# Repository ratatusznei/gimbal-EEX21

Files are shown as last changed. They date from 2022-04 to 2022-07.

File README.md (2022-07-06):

# Sistema estabilizador de dois eixos para câmera - Gimbal

###### Autores em ordem alfabética
[Fernando](https://github.com/ratatusznei)

[Henrique](https://github.com/HenriqueKnapp)

[Robson](https://github.com/robson1622)

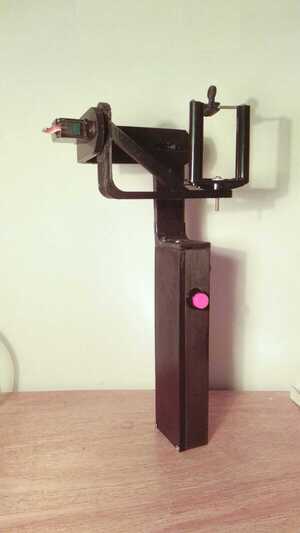
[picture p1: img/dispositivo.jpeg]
Dispositivo montado sem celular


Foto do dispositivo montado sem o celular no suporte.

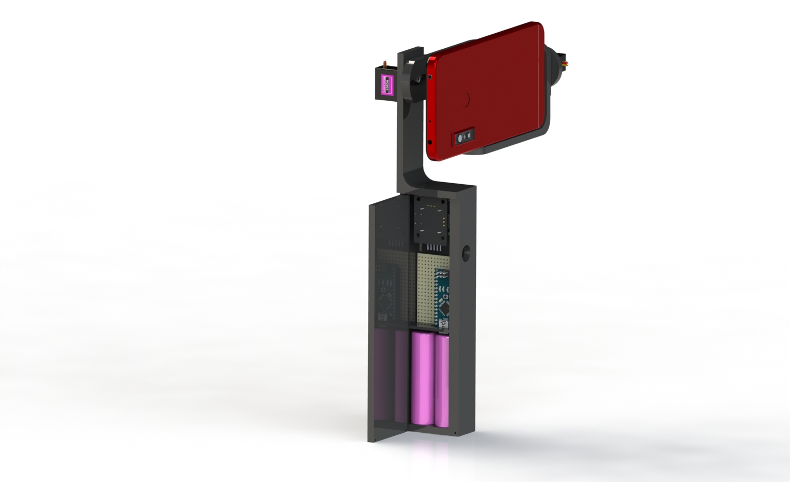
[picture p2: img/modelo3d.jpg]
Modelo 3d


Renderização de modelo montado em computador, mostrando a placa de circuitos e as baterias internas.

## O que é?
É um dispositivo que procura manter a orientação de uma câmera ou celular fixa, compensando possíveis variações que podem ocorrer durante a gravação de um vídeo ou fotografia. O sistema estabiliza nos eixos X e Y conforme a figura:

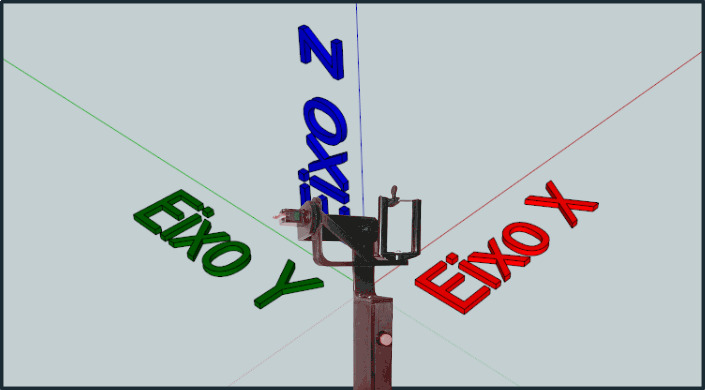
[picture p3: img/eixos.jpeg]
Estabilizador no espaço 3d Eixos de atuação X e Y


## Como funciona?
O sistema contrói uma representação interna da orientação do dispositivo em relação à direção da gravidade com base nas leituras de dois sensores giroscópio e acelerômetro. Então utilizando de dois motores atuando sobre a orientação da câmera a gravação é estabilizada.

## Casos de uso
Além de servir como estabilizador para câmeras, esse sistema pode ser readequado para uso em robôs sensíveis à orientação, drones ou em aplicações de realidade virtual capturando a orientação de um objeto no mundo real.

## Mais detalhes
Para mais detalhes e referências sobre o projeto, verifique o [relatório final nesse mesmo repositório](https://github.com/ratatusznei/gimbal-EEX21/blob/master/relatorio/pdfs/EEX21_Equipe5_Relatorio_EstabilizadorDeDoisEixosPraCameras.pdf).

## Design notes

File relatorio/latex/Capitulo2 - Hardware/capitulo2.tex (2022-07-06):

%%%% CAPÍTULO 2 - REVISÃO DA LITERATURA (OU REVISÃO BIBLIOGRÁFICA, ESTADO DA ARTE, ESTADO DO CONHECIMENTO)
%%
%% O autor deve registrar seu conhecimento sobre a
%% literatura básica do assunto, discutindo e 
%% comentando a informação já publicada. A revisão deve
%% ser apresentada, preferencialmente, em ordem
%% cronológica e por blocos de assunto, procurando
%% mostrar a evolução do tema.

%% Título e rótulo de capítulo (rótulos não devem conter caracteres especiais, acentuados ou cedilha)
\chapter{Hardware}\label{cap:revisaodaliteratura}

 Para a construção do projeto, foram utilizados os componentes listados na tabela 1, além de ferramentas como ferro de solda, percloreto de ferro etc.

\begin{table}[H]
\centering
\begin{tabular}{l|j|j}
Componente & Modelo/especificações & Quantidade \\\hline
Arduino & Nano & 1 \\
Baterias recarregáveis & INR18650-30Q & 2\\
ServoMotores & MG90s & 2\\
Joystick analógico & 3 Eixos KY-023 & 1\\
Interruptor Push Button & Retenção PBS-11A (127v) & 1\\
Regulador de tensão & LM7805 & 1\\
Acelerômetro e giroscópio & MPU-6050 & 1\\
Dissipador de alumínio & & 1\\
Barramentos & Macho e Fêmea 10 cm & 2\\
Cabo flat & 10 vias, 20 cm & 1\\
Espaguete termo retrátil & 20 cm & 1\\
Placa de fenolite & (Não perfurada) & 1\\ 
Filamento para impressora 3D & & \\
Parafusos & 8 mm & 10\\
\end{tabular}
\caption{\label{tab:widgets}Tabela de componentes e materiais utilizados na construção do dispositivo.}
\end{table}

\section{Modelagem e impressão 3D}
Todo o hardware do dispositivo está montado em uma estrutura impressa em 3D, as peças da estrutura da caixa (paredes e tampa) foram impressas ocas e com o filamento PLA que é mais frágil e leve se comparado ao material utilizado na impressão do suporte articulado, as peças do suporte articulado foram reforçadas sendo parcialmente impressas de forma maciça e produzidas com o filamento ABS ,que apresenta maior resistência, isto para suportar o peso do equipamento que será anexado à base da estrutura articulada. As dimensões das peças impressas em 3d foram definidas a partir de modelos dos componentes e também do circuito produzidos no software KiCad e SolidWorks, como pode ser visto nas figuras 1 e 2. 

\begin{figure}[H]
\centering
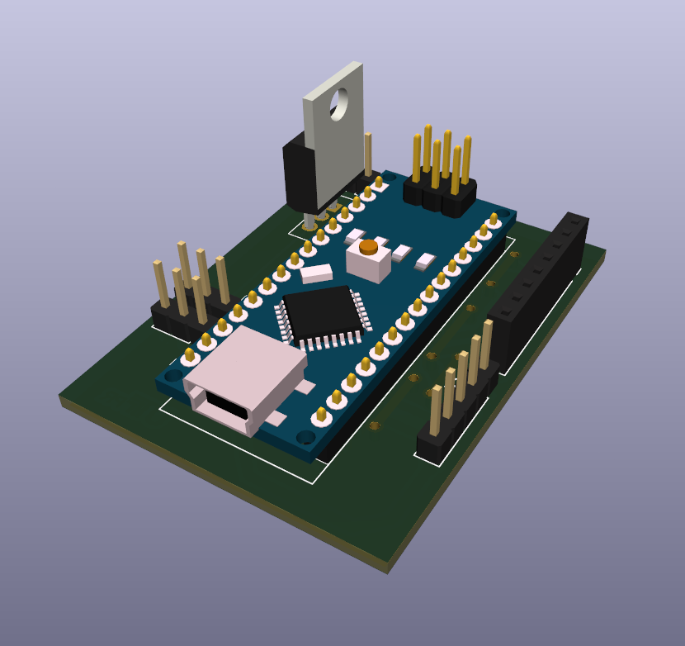
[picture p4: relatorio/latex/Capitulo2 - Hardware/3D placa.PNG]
\\
\caption{\label{fig:widgets}Modelo 3D da placa de circuito impresso.}
\end{figure}

\begin{figure}[H]
\centering
\\
\caption{\label{fig:widgets}Modelo 3D do dispositivo.}
\end{figure}

\section{Suporte articulado}
A estabilização para o equipamento preso à estrutura articulada é dada por dois eixos de rotação, estes possibilitam variar a inclinação do suporte na vertical e na horizontal de zero a 90 graus para cada lado, isto devido a cada servo motor MG90s possibilitar uma rotação de 180 graus. Cada servo motor opera entre 4,8 e 6 volts, com seu torque e velocidade de operação variando de acordo com esses parâmetros. Para um funcionamento estável, os motores não são alimentados pelo arduino, a tensão máxima fornecida aos dois servos é de 5 volts, como a tensão de saída do conjunto de baterias é de 7,2 volts, foi utilizado um regulador de tensão LM7805, que mantém uma tensão estável de 5 volts se a tensão de entrada for maior que 7 volts, não excedendo 30 volts, isso nos dá os parâmetros da tabela 2.

\begin{table}[H]
\centering
\begin{tabular}{j|j|j}
Tensão de entrada & Torque & Velocidade de operação \\\hline
4,8 & 1,8kg/cm & 0.1sec/60 graus\\
5,0 & 1,9kg/cm & 0.1sec/60 graus\\
6,0 & 2,2kg/cm & 0.08sec/60 graus\\
\end{tabular}
\caption{\label{tab:widgets}Tabela de parâmetros do servo motor MG90s para diferentes tensões de entrada.}
\end{table}

Ambos os servos são fixados diretamente na estrutura impressa por meio de dois parafusos, e as peças móveis da estrutura articulada são encaixadas diretamente no eixo de cada um dos servos com o auxilio de hélices de plástico. Para facilitar a movimentação das partes móveis e diminuir o atrito, e por consequência o desgaste do material plástico, foi adicionado sob cada eixo (encontro de duas partes móveis) duas arruelas de ferro com graxa. O cabeamento dos dois servos segue presa às estruturas móveis da estrutura articulada, isso devido ao comprimento necessário dos cabos ser diferente para diferentes posições de operação.

\section{Eletrônica}
%incluir esquematico, diagrama de blocos
O sistema conta com duas células (baterias) recarregáveis de 3,6 volts e 3000 mAh ligadas em série, fornecendo ao sistema 7,2 volts, este conjunto de baterias é ligado a um interruptor, e este é ligado à placa de circuitos. A trilha positiva se liga ao regulador de tensão LM7805 (que manda cerca de 5,0 volts aos dois servo motores), e também ao arduino nano (este não precisa de um regulador de tensão externo, como no caso dos dois servos, pois já possui um integrado em sua placa). O joystick analógico e o sensor MPU-6050 são conectados exclusivamente ao arduino conforme pode ser visto na figura 3. Todos os componentes são conectados por meio de barramentos soldados na placa, permitindo o funcionamento como pode ser visto na figura 4, dando ao sistema modularidade, uma vez que cada componente pode ser removido individualmente, facilitando operações como manutenção e ajustes.

\begin{figure}[H]
\centering
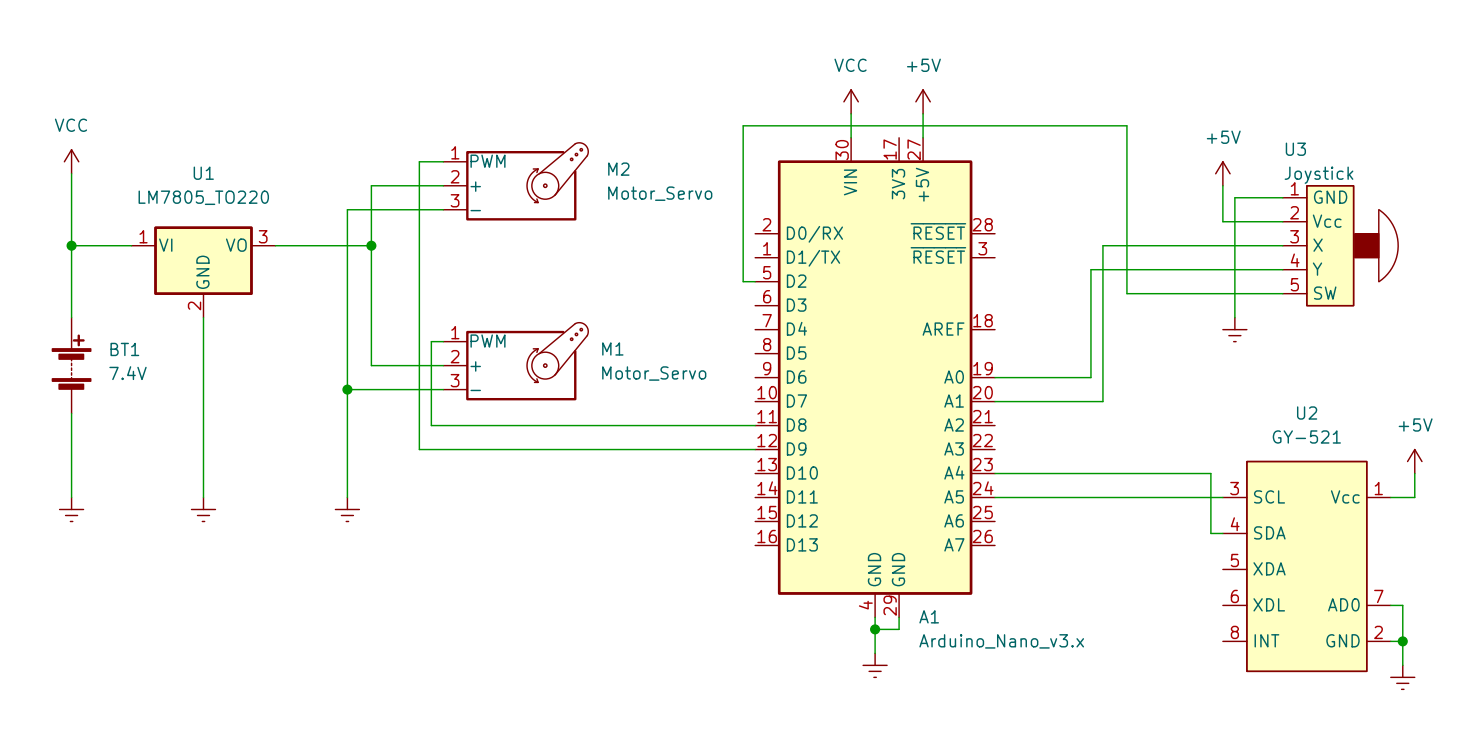
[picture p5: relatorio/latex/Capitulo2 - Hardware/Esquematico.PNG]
\\
\caption{\label{fig:widgets}Esquemático dos componentes eletrônicos.}
\end{figure}

\begin{figure}[H]
\centering
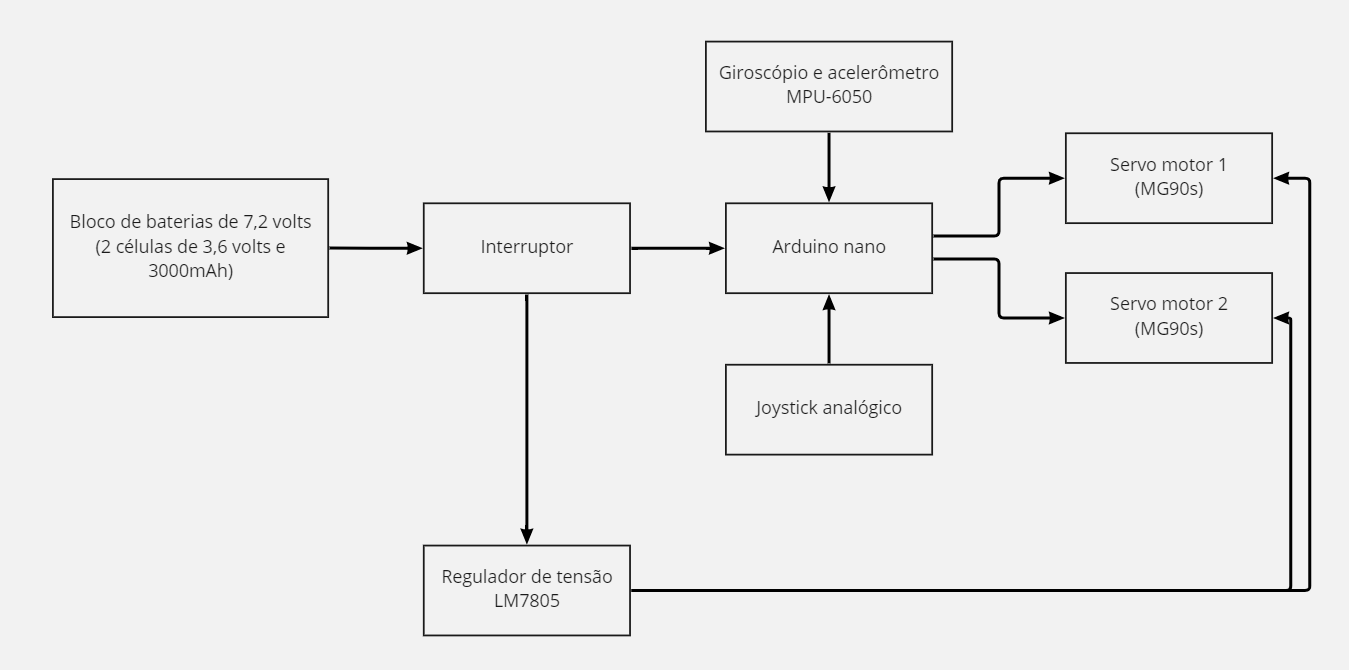
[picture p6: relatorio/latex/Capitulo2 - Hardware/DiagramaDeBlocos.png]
\\
\caption{\label{fig:widgets}Diagrama de blocos do dispositivo.}
\end{figure}

A placa de circuitos foi produzida manualmente pelos integrantes do grupo deste trabalho utilizando percloreto de ferro. A imagem do circuito foi produzida através do software KiCad, como pode ser visto na figura 5, e foi transferida de um papel fotográfico para a placa de fenolite utilizando uma fonte de calor, depois de resfriada, foi imersa em percloreto de ferro por cerca de cinco minutos. Após o fim do processo, obtivemos uma placa funcional do circuito do projeto, como pode ser visto na figura 6.

\begin{figure}[H]
\centering
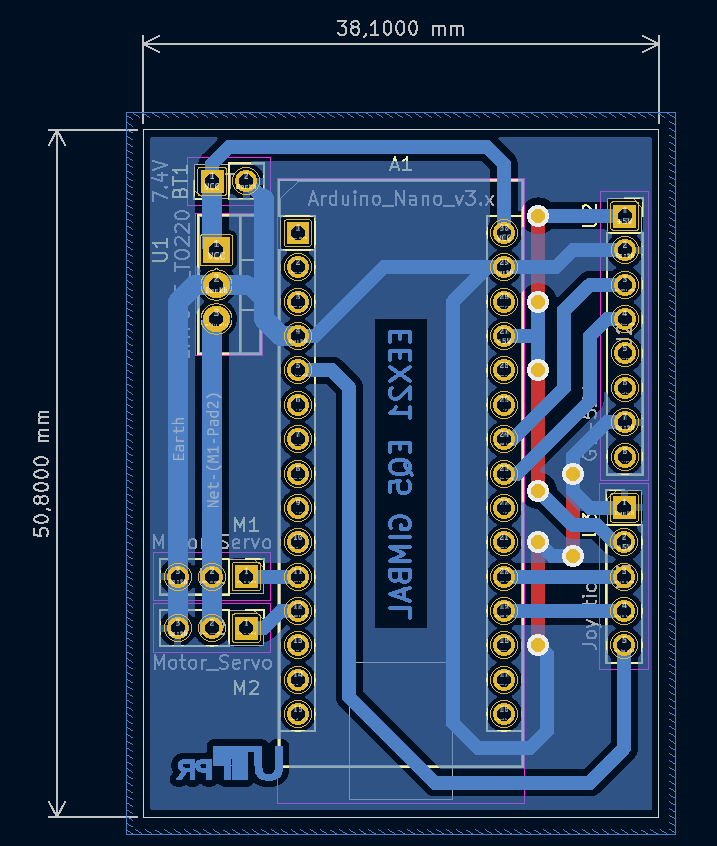
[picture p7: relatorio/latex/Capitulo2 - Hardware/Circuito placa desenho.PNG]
\\
\caption{\label{fig:widgets}Desenho do circuito no software KiCad.}
\end{figure}

\begin{figure}[H]
\centering
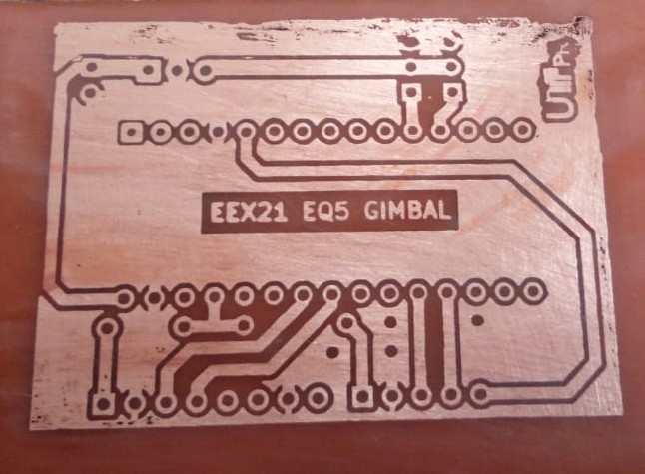
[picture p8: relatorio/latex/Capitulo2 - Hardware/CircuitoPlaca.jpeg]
\\
\caption{\label{fig:widgets}Placa produzida manualmente utilizando o processo de corrosão por percloreto de ferro.}
\end{figure}

Com exceção dos servo motores, os componentes são posicionados dentro da estrutura impressa (caixa) através de pequenos parafusos, dando espaço ao posicionamento do módulo MPU-6050 com sua placa orientada na horizontal, nos permitindo obter leituras precisas da inclinação nos dois eixos de rotação da estrutura articulada, como também possibilitar a passagem dos cabos sem prejudicar outros componentes.

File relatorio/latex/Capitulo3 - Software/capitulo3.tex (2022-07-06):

%%%% CAPÍTULO 3 - MATERIAL E MÉTODOS (PODE SER OUTRO TÍTULO DE ACORDO COM O TRABALHO REALIZADO)
%%
%% Deve apresentar o modelo utilizado, a modelagem
%% empregada, as simplificações necessárias, a
%% metodologia e a descrição do método de cálculo 
%% utilizado no desenvolvimento da pesquisa para que
%% a mesma possa ser reconstituída. Deve ainda 
%% apresentar resultados de amostras e comentários.
%% Deve apresentar a descrição da montagem 
%% experimental, metodologia para a obtenção de 
%% resultados, análise de erros, amostra de resultados
%% obtidos e comentários. Atenção: Esta parte pode ser
%% subdividida em mais capítulos de acordo com a 
%% especificidade do assunto.

%% Título e rótulo de capítulo (rótulos não devem conter caracteres especiais, acentuados ou cedilha)
\chapter{Software}\label{cap:materialemetodos}

\section{Ferramentas e Bibliotecas}
O código do controlador foi feito utilizando o IDE do arduino e as bibliotecas "MPU6050\textunderscore light" e "Servo", disponíveis para download pelo IDE. A primeira biblioteca realiza a leitura dos sensores acelerômetro e giroscópio pelo barramento I2C do arduino, além de combiná-los com um filtro complementar que será explicado a seguir. A segunda biblioteca realiza o controle das posições dos servo motores por meio de um sinal PWM. Uma visão geral do funcionamento do sistema é dada pelo fluxograma na figura 7.

\begin{figure}[H]
\centering
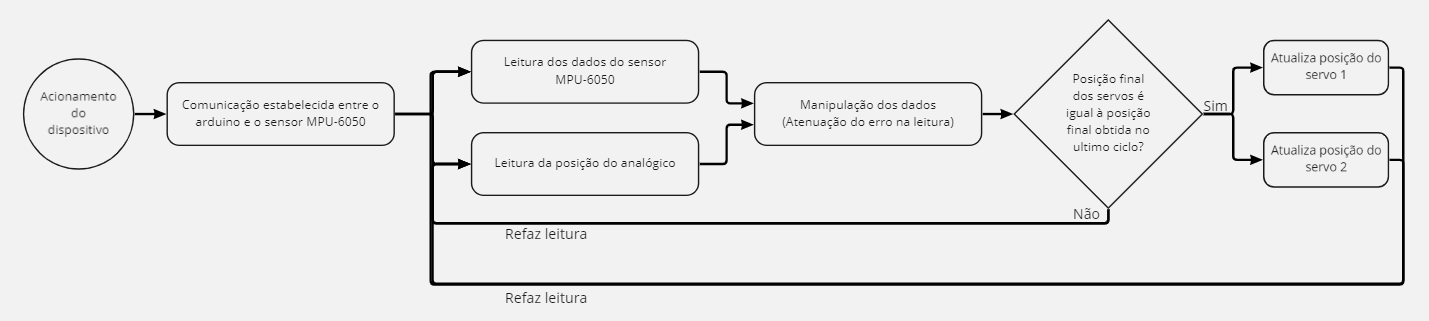
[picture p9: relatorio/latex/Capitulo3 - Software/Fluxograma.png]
\\
\caption{\label{fig:widgets}Fluxograma da sequencia de operação do sistema.}
\end{figure}

\section{Ângulos a partir das leituras do MPU-6050}
A leitura dos sensores é realizada pela biblioteca "MPU6050\textunderscore light", são lidos utilizando o protocolo I2C os valores brutos da aceleração linear, do acelerômetro, e angular, do giroscópio.\\
\indent Em funcionamento normal a maior aceleração linear percebida pelo dispositivo é a gravidade e, com um pouco de trigonometria, é calculada a rotação do sistema em relação à direção "para baixo". Ao longo do tempo o valor médio calculado se mantém próximo do esperado, porém qualquer movimento, até mesmo as vibrações de origem térmica no material, causam ruídos e ainda não podemos utilizar essa leitura diretamente.\\
\indent Das leituras da aceleração angular podemos integrar o sinal duas vezes para obter a velocidade angular e então o ângulo relativo à alguma posição de referência. Para um tempo curto essa leitura já basta, contudo o erro do sistema é somado em cada ciclo de integração e um desvio vai se acumulando com o tempo. Outro problema que precisa ser corrigido antes de utilizar essa leitura é a definição dessa posição de referência.\\
\\
\indent Pode-se observar então que temos uma variável com boa confiança em curto prazo (do giroscópio) e outra cuja a confiança é aceitável apenas após a coleta de várias leituras após um longo tempo para ser calculada uma média (do acelerômetro). Pode-se então utilizar a técnica de filtros complementares para combinar o sinal dos dois sensores e ter o melhor dos dois mundos. A figura 8 apresenta um diagrama em blocos do filtro implementado pela biblioteca. O parâmetro k controla qual medição vai ter mais influência em curto prazo e, por complemento, qual teria mais influência após um tempo muito longo. Valores típicos são cerca 99\%, dando um peso maior para as leituras de ângulo pelo giroscópio em curto prazo e para o acelerômetro, que vai fazer o trabalho da posição de referência, após muito tempo.

\begin{figure}[H]
\centering
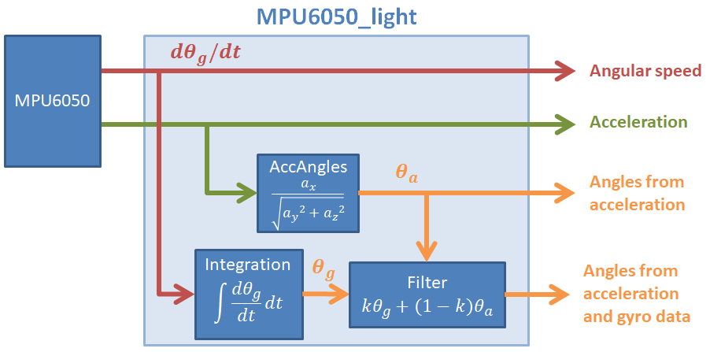
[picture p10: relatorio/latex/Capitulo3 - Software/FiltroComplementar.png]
\\
\caption{\label{fig:widgets}Operação do filtro - Imagem obtida na documentação da biblioteca "MPU6050\textunderscore light"}
\end{figure}

\section{Testes sem a estrutura 3D}

Durante o desenvolvimento do projeto foi utilizada uma aplicação web 3d para testes com sensor MPU-6050, que nos permitiu analisar seu funcionamento sem ter de acoplar motores ou quaisquer outros atuadores, tal aplicação é executada no navegador Chrome ou semelhante do computador, sendo necessário somente que o sensor esteja ligado a um arduino, e este arduino, ligado ao computador. Ao iniciar a aplicação, é solicitada a porta serial conectada ao sistema com o sensor, com isso, a interface fornece um cubo, como mostrado na figura 9, que acompanha a rotação do sensor no mundo real.

\begin{figure}[H]
\centering
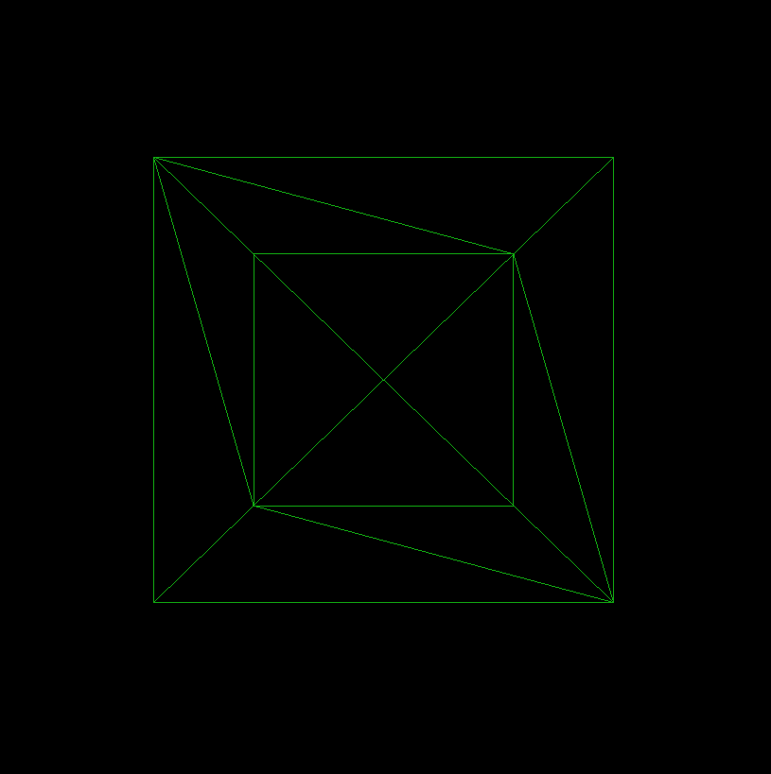
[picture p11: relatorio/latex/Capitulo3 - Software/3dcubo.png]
\\
\caption{\label{fig:widgets}Fluxograma da sequencia de operação do sistema.}
\end{figure}

\section{Leitura do Joystick}
No joystick é feito três leituras, o eixo x, eixo y e um botão de reset. Os eixos de movimento são lidos direto por portas analógicas no arduino e o botão por uma porta digital.\\
\indent O joystick controla um ajuste para cada eixo, esses ajustes são dois ângulos de desvio a ser considerados no posicionamento dos motores. Movendo um eixo do joystick para uma posição positiva o ajuste correspondente é incrementado com o tempo. O simétrico vale para uma posição negativa também. Podemos imaginar um plano "Ajuste X x Ajuste Y" com um ponto cujas as coordenadas são um ajuste final, o joystick então movimentaria esse ponto como se fosse um personagem de um jogo.

\pagebreak
\section{Controle dos servomotores}

Os servomotores são controlados por um sinal modulado por largura de pulso (PWM). O período do sinal é de 20ms e a largura de pulso varia entre 1ms e 2ms, que posicionam o servo nas posições 0º e 180º, respectivamente. Para poupar tempo de desenvolvimento foi utilizada a biblioteca "Servo" que gera essas formas de onda.\\
\indent Da saída do filtro complementar já temos um bom posicionamento, mas ainda causa solavancos extremos em quase todo movimento. Antes de enviar a nova posição de correção para os servos esse sinal ainda é tratado com um filtro de média levando em conta os últimos 5 valores e é adicionado o valor de ajuste do joystick. Então a posição do servomotor é interpolada entre a posição antiga e a nova posição corrigida. Dessa forma no começo de uma correção os motores se movimentam rapidamente e conforme se aproximam da posição final eles desaceleram, reduzindo os solavancos.

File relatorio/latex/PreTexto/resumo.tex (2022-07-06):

%%%% RESUMO
%%
%% Apresentação concisa dos pontos relevantes de um texto, fornecendo uma visão rápida e clara do conteúdo e das conclusões do trabalho.

\begin{resumoutfpr}%% Ambiente resumoutfpr
ESTABILIZADOR DE DOIS EIXOS PARA CÂMERAS. 18f. Oficina de Integração 1 - Relatório Final - Curso de Engenharia de Computação, UNIVERSIDADE TECNOLÓGICA FEDERAL DO PARANÁ (UTFPR). Curitiba, 2022.\\\\O presente documento descreve um dispositivo destinado à estabilização de câmeras por meio de uma estrutura articulada. O projeto foi idealizado visando atender uma necessidade específica do ramo audiovisual, a grande maioria das câmeras ainda em atuação no mercado não possuem mecanismos de supressão à vibrações, sendo muito perceptível em suas gravações, trepidações que, rotineiramente, obrigam à realização de novas gravações ou a perda do material gravado devido à baixa qualidade. Com o objetivo de diminuir o problema, foi criado um dispositivo que cancela grandes vibrações utilizando dois motores servo e um micro controlador Arduino nano, tal dispositivo opera sobre dois eixos, alterando a inclinação vertical e horizontal de uma estrutura articulada, que, por fim, estabiliza o dispositivo de vídeo que é anexado a ela.

\end{resumoutfpr}

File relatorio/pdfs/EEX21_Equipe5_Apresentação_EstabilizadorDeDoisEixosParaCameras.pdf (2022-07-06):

# Estabilizador de dois eixos para câmeras

Oficina de Integração 1 - Engenharia de Computação UTFPR

Por:
Henrique Francisco Knapp
Fernando Henrique Ratusznei Caetano Robson Borges dos Santos

# Definição e conceito de projeto

Um estabilizador para câmeras é um dispositivo que, a partir de sensores e atuadores, move uma estrutura articulada, na qual é fixado um dispositivo de vídeo, de modo a anular vibrações e variações na inclinação vertical e horizontal, permitindo realizar uma gravação estável.

Utilizando um microcontrolador arduino nano:

- Controlar uma estrutura articulada que possibilite correções de inclinação nos eixos vertical e horizontal.
- Permitir a mudança de orientação da estrutura articulada através de um joystick analógico.

# Hardware

O sistema é composto por:
- 2 servo motores + 1 regulador de tensão
- 1 arduino nano
- 1 joystick analógico
- 1 giroscópio e acelerômetro MPU-6050
- 1 conjunto de baterias de 7,2 volts

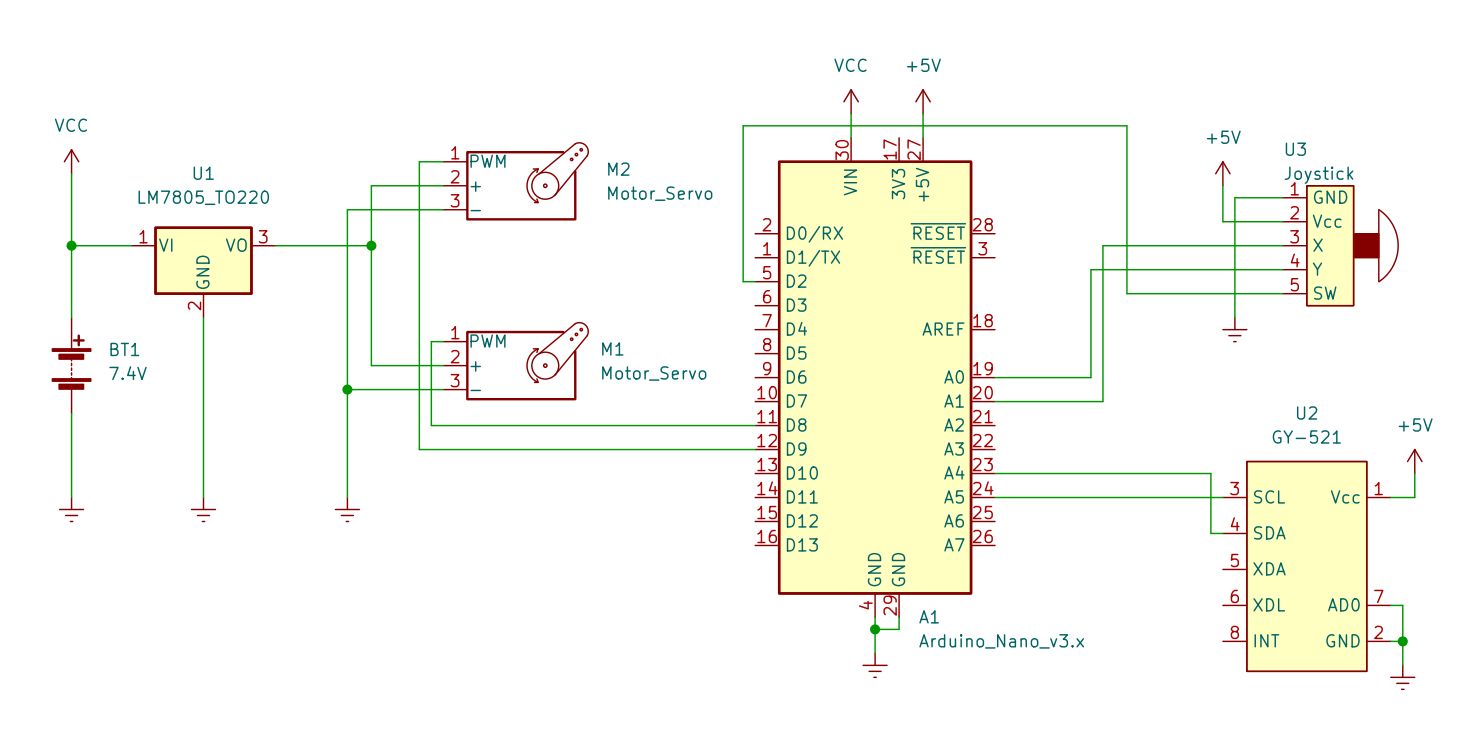
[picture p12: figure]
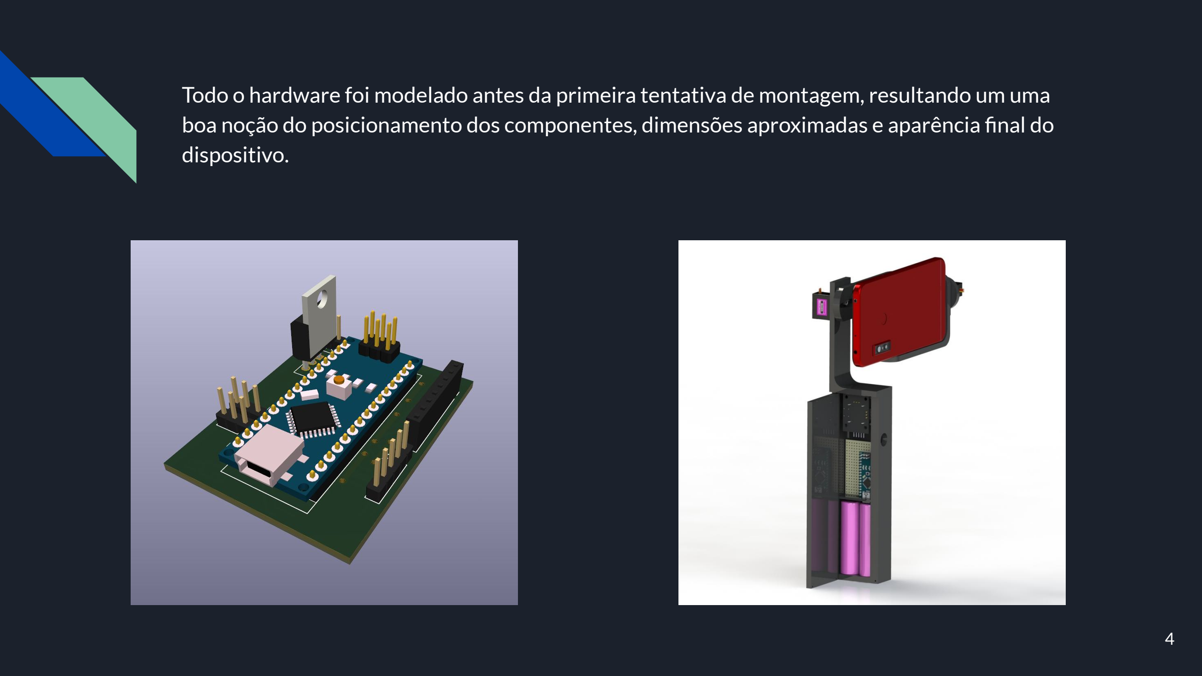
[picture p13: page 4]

Todo o hardware foi modelado antes da primeira tentativa de montagem, resultando um uma boa noção do posicionamento dos componentes, dimensões aproximadas e aparência final do dispositivo.

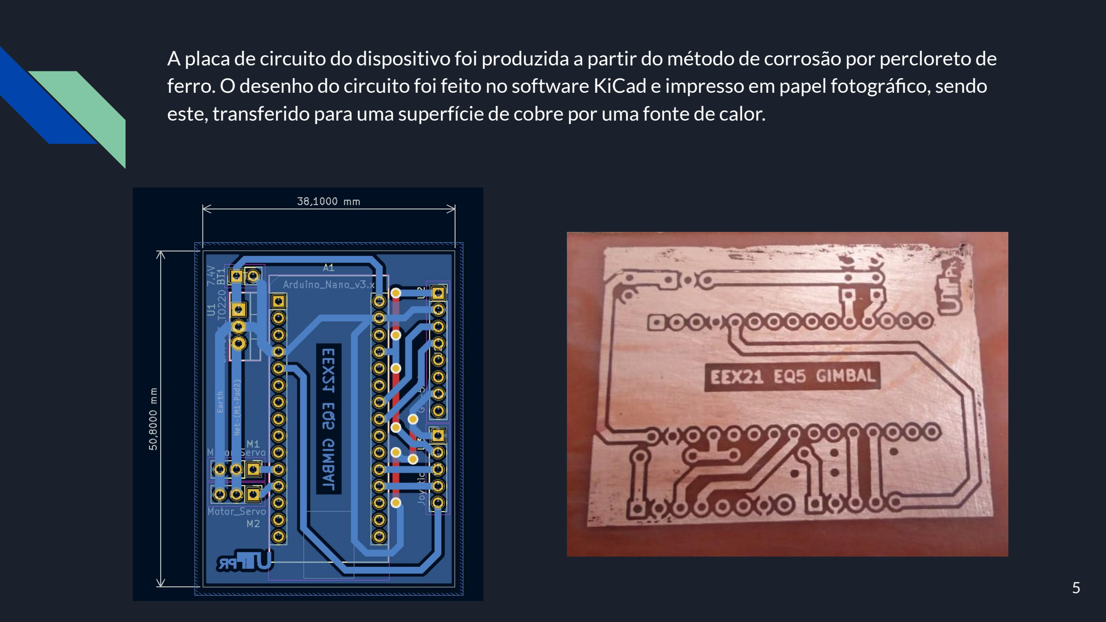
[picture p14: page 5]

A placa de circuito do dispositivo foi produzida a partir do método de corrosão por percloreto de ferro. O desenho do circuito foi feito no software KiCad e impresso em papel fotográfico, sendo este, transferido para uma superfície de cobre por uma fonte de calor.

# Software

Uma vez acionado, o dispositivo realiza a leitura de dados do sensor MPU-6050 e do joystick analógico. Com base nestes dados, o software verifica se é necessário atualizar a posição dos motores para manter o suporte anexado à estrutura articulada estabilizado.

O joystick analógico tem a função de possibilitar a mudança de orientação da estrutura articulada, ou seja, alterar a inclinação vertical e horizontal.

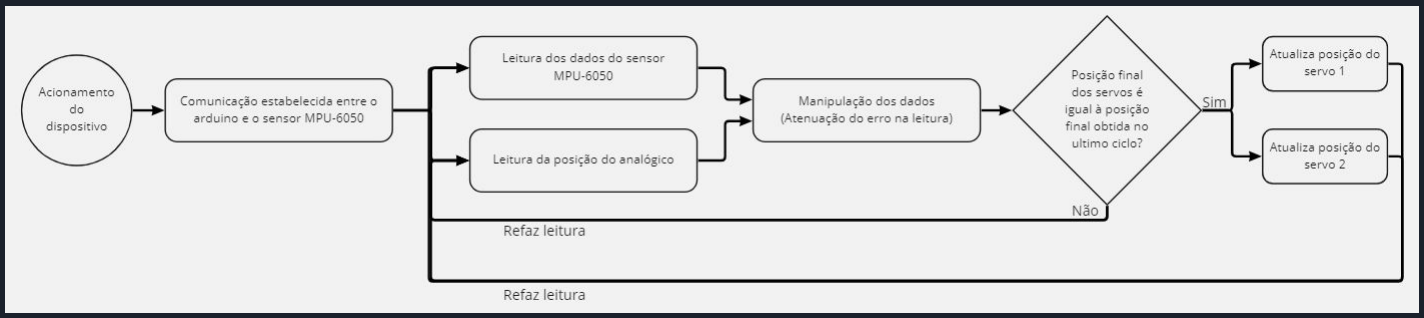
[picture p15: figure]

Os dados obtidos do módulo MPU-6050 são leituras do giroscópio (aceleração angular) e do acelerômetro (aceleração linear).

Do giroscópio obtemos uma leitura de confiança a curto prazo (um erro de leitura é somado a cada novo ciclo do programa).

Do acelerômetro obtemos valores confiáveis após a coleta de várias leituras para que seja calculada uma média.

Utilizando filtros complementares, combinamos o sinal dos dois sensores e obtemos a leitura que será utilizada para a atualização da posição dos motores.

# Fotos

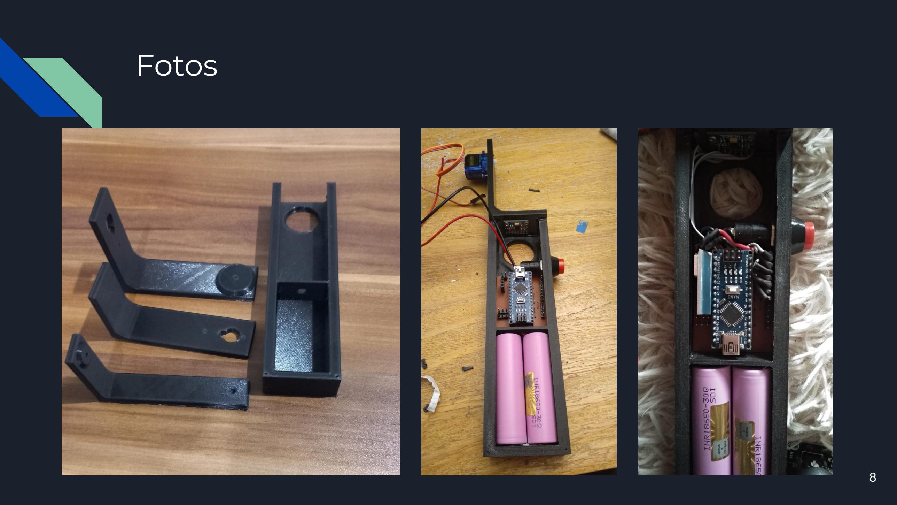
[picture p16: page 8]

# Conclusões

Apesar de utilizarmos uma aplicação 3D para o entendimento do funcionamento do módulo MPU-6050, sua integração se mostrou complicada, devido a necessidade de criação de um algoritmo que unisse leituras de dois sensores diferentes de um mesmo módulo a fim de obter valores confiáveis.

A existência de partes móveis acopladas, a princípio, gerou problemas de estabilidade e resistência, o que ocasionou o retrabalho de algumas peças e a perda de outras. O problema foi solucionado utilizando filamentos mais resistentes para as impressões 3D e também o aprimoramento dos modelos 3D.

# Resultado final

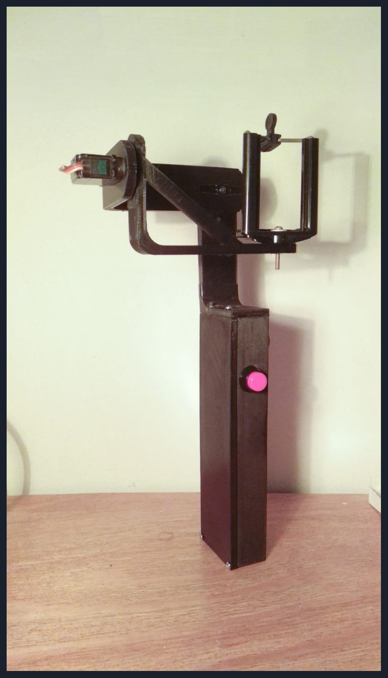
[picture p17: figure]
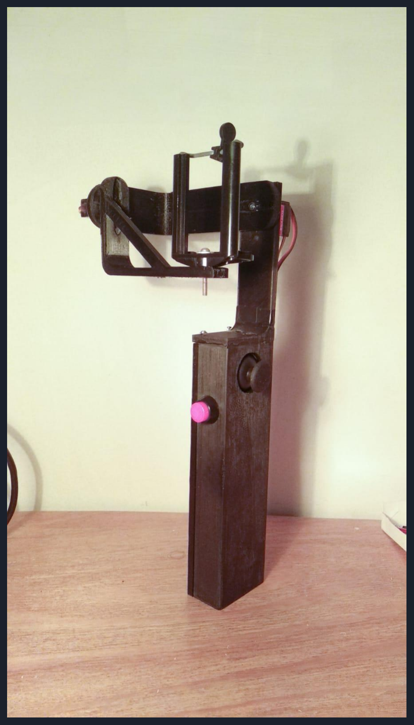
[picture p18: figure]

# OBRIGADO

Estabilizador de dois eixos para câmeras. (https://youtu.be/y9m5s8JzXt0)

Vídeo do projeto:

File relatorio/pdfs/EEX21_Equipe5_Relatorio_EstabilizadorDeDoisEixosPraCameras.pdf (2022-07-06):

UNIVERSIDADE TECNOLÓGICA FEDERAL DO PARANÁ

CURSO DE ENGENHARIA DE COMPUTAÇÃO

HENRIQUE FRANCISCO KNAPP

FERNANDO HENRIQUE RATUSZNEI CAETANO

ROBSON BORGES DOS SANTOS

### ESTABILIZADOR DE DOIS EIXOS PARA CÂMERAS

OFICINA DE INTEGRAÇÃO 1 - RELATÓRIO FINAL

CURITIBA

2022

HENRIQUE FRANCISCO KNAPP

FERNANDO HENRIQUE RATUSZNEI CAETANO

ROBSON BORGES DOS SANTOS

### ESTABILIZADOR DE DOIS EIXOS PARA CÂMERAS

Relatório final do projeto desenvolvido na disciplina de Oficina de Integração 1, do curso de Engenharia de Computação, da Universidade Tecnológica Federal do Paraná (UTFPR).

Orientadores:
Prof. Juliano Mourão Vieira. Prof. Ronnier Frates Rohrich

CURITIBA

2022

RESUMO

ESTABILIZADOR DE DOIS EIXOS PARA CÂMERAS. 18f. Oficina de Integração 1 -Relatório Final - Curso de Engenharia de Computação, UNIVERSIDADE TECNOLÓGICA FEDERAL DO PARANÁ (UTFPR). Curitiba, 2022.

O presente documento descreve um dispositivo destinado à estabilização de câmeras por meio de uma estrutura articulada. O projeto foi idealizado visando atender uma necessidade específica do ramo audiovisual, a grande maioria das câmeras ainda em atuação no mercado não possuem mecanismos de supressão à vibrações, sendo muito perceptível em suas gravações, trepidações que, rotineiramente, obrigam à realização de novas gravações ou a perda do material gravado devido à baixa qualidade. Com o objetivo de diminuir o problema, foi criado um dispositivo que cancela grandes vibrações utilizando dois motores servo e um micro controlador Arduino nano, tal dispositivo opera sobre dois eixos, alterando a inclinação vertical e horizontal de uma estrutura articulada, que, por fim, estabiliza o dispositivo de vídeo que é anexado a ela.

Palavras-chave: Estabilizador para câmeras. Servo motores. Suporte articulado. Manipulação de dados com arduino.

SUMÁRIO

### 1 INTRODUÇÃO

1.1 MOTIVAÇÃO

Um recurso que está começando a se tornar popular em dispositivos de captura de

vídeo apenas recentemente é a estabilização mecânica. Para pequenas vibrações, a estabilização

eletrônica ou digital (já existente a alguns anos) já é suficiente para melhorar a qualidade de

fotos, esta é feita via software, através de um algoritmo que tenta minimizar a vibração do

dispositivo, no entanto, sua aplicação para vídeos ainda apresenta alguns problemas, uma vez

que tal estabilização exige que cada quadro do vídeo seja trabalhado de forma diferente pelo

algoritmo, de modo que a gravação final tenha uma boa estabilização, o que pode custar muito

do processamento de um dispositivo. Outro mecanismo existente é a estabilização óptica, que,

através de sensores embutidos no dispositivo, identifica os movimentos realizados, e através de

pequenos motores, ajusta a posição das lentes de modo a obter imagens mais estáveis durante

a gravação. Esta é uma solução melhor que a típica estabilização digital presente na maioria

dos dispositivos de gravação, como celulares e pequenas câmeras, mas ainda é um recurso

com limitações, e para dar a um dispositivo a melhor estabilização possível, foi criado um

equipamento externo para realizar esta função.

A estabilização mecânica realizada por um dispositivo externo não possui as limitações

de movimentação do dispositivo de gravação, mesmo que a base onde o estabilizador externo é

fixado se mova, sua estrutura articulada realiza os movimentos contrários aos realizados pela

base, anulando os movimentos e deixando o dispositivo anexado a esta estrutura estabilizado.

Este é um recurso caro e economicamente indisponível para a grande parte das pessoas.

1.2 OBJETIVOS

1.2.1 Objetivo geral

Criação de um dispositivo de estabilização externa que possua uma estrutura articulada

que se movimente em dois eixos, de modo a deixar sua base acoplada, estabilizada, e como

consequência, o dispositivo de vídeo anexado a esta base, também estabilizado. Tal equipamento

deve ser composto por atuadores e sensores acoplados à um microcontrolador Arduino.

1.2.2 Objetivos específicos

- O equipamento deve operar com baterias, estas devem ser carregadas externamente.
- O equipamento deve estabilizar uma base através da movimentação de dois eixos de

rotação, um eixo mantendo a inclinação vertical, e outro eixo mantendo a inclinação

horizontal.

- O equipamento deve permitir a mudança de orientação da base (onde é fixado o dispositivo

externo) através de um joystick analógico, com o switch tendo a função de posicionar a

base de volta a posição original.

- A base presa à estrutura articulada deve possibilitar anexar um smartphone ou uma câmera

externa com peso de até 300 gramas, sendo esse valor definido pela resistência tolerada

pela estrutura impressa.

- Deve ser feita uma placa de circuito específica para o dispositivo.
- A estrutura do equipamento deve ser produzida por uma impressora 3D.

### 2 HARDWARE

Para a construção do projeto, foram utilizados os componentes listados na tabela 1,

além de ferramentas como ferro de solda, percloreto de ferro etc.

Componente | Modelo/especificações | Quantidade
Arduino | Nano | 1
Baterias recarregáveis | INR18650-30Q | 2
ServoMotores | MG90s | 2
Joystick analógico | 3 Eixos KY-023 | 1
Interruptor Push Button | Retenção PBS-11A (127v) | 1
Regulador de tensão | LM7805 | 1
Acelerômetro e giroscópio | MPU-6050 | 1
Dissipador de alumínio | | 1
Barramentos | Macho e Fêmea 10 cm | 2
Cabo flat | 10 vias, 20 cm | 1
Espaguete termo retrátil | 20 cm | 1
Placa de fenolite | (Não perfurada) | 1
Filamento para impressora 3D
Parafusos | 8 mm | 10

Tabela 1 – Tabela de componentes e materiais utilizados na construção do dispositivo.

2.1 MODELAGEM E IMPRESSÃO 3D

Todo o hardware do dispositivo está montado em uma estrutura impressa em 3D, as

peças da estrutura da caixa (paredes e tampa) foram impressas ocas e com o filamento PLA que

é mais frágil e leve se comparado ao material utilizado na impressão do suporte articulado, as

peças do suporte articulado foram reforçadas sendo parcialmente impressas de forma maciça e

produzidas com o filamento ABS ,que apresenta maior resistência, isto para suportar o peso do

equipamento que será anexado à base da estrutura articulada. As dimensões das peças impressas

em 3d foram definidas a partir de modelos dos componentes e também do circuito produzidos no

software KiCad e SolidWorks, como pode ser visto nas figuras 1 e 2.


Figura 1 – Modelo 3D da placa de circuito impresso.

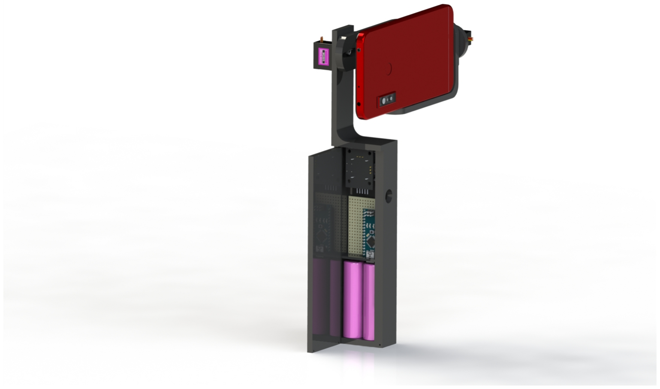
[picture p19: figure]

Figura 2 – Modelo 3D do dispositivo.

2.2 SUPORTE ARTICULADO

A estabilização para o equipamento preso à estrutura articulada é dada por dois eixos

de rotação, estes possibilitam variar a inclinação do suporte na vertical e na horizontal de zero

a 90 graus para cada lado, isto devido a cada servo motor MG90s possibilitar uma rotação de

180 graus. Cada servo motor opera entre 4,8 e 6 volts, com seu torque e velocidade de operação

variando de acordo com esses parâmetros. Para um funcionamento estável, os motores não são

alimentados pelo arduino, a tensão máxima fornecida aos dois servos é de 5 volts, como a tensão

de saída do conjunto de baterias é de 7,2 volts, foi utilizado um regulador de tensão LM7805, que mantém uma tensão estável de 5 volts se a tensão de entrada for maior que 7 volts, não

excedendo 30 volts, isso nos dá os parâmetros da tabela 2.

Tensão de entrada | Torque | Velocidade de operação
4,8 | 1,8kg/cm | 0.1sec/60 graus
5,0 | 1,9kg/cm | 0.1sec/60 graus
6,0 | 2,2kg/cm | 0.08sec/60 graus

Tabela 2 – Tabela de parâmetros do servo motor MG90s para diferentes tensões de entrada.

Ambos os servos são fixados diretamente na estrutura impressa por meio de dois

parafusos, e as peças móveis da estrutura articulada são encaixadas diretamente no eixo de cada

um dos servos com o auxilio de hélices de plástico. Para facilitar a movimentação das partes

móveis e diminuir o atrito, e por consequência o desgaste do material plástico, foi adicionado sob

cada eixo (encontro de duas partes móveis) duas arruelas de ferro com graxa. O cabeamento dos

dois servos segue presa às estruturas móveis da estrutura articulada, isso devido ao comprimento

necessário dos cabos ser diferente para diferentes posições de operação.

2.3 ELETRÔNICA

O sistema conta com duas células (baterias) recarregáveis de 3,6 volts e 3000 mAh

ligadas em série, fornecendo ao sistema 7,2 volts, este conjunto de baterias é ligado a um

interruptor, e este é ligado à placa de circuitos. A trilha positiva se liga ao regulador de tensão

LM7805 (que manda cerca de 5,0 volts aos dois servo motores), e também ao arduino nano

(este não precisa de um regulador de tensão externo, como no caso dos dois servos, pois já

possui um integrado em sua placa). O joystick analógico e o sensor MPU-6050 são conectados

exclusivamente ao arduino conforme pode ser visto na figura 3. Todos os componentes são

conectados por meio de barramentos soldados na placa, permitindo o funcionamento como pode

ser visto na figura 4, dando ao sistema modularidade, uma vez que cada componente pode ser

removido individualmente, facilitando operações como manutenção e ajustes.


Figura 3 – Esquemático dos componentes eletrônicos.


Figura 4 – Diagrama de blocos do dispositivo.

A placa de circuitos foi produzida manualmente pelos integrantes do grupo deste

trabalho utilizando percloreto de ferro. A imagem do circuito foi produzida através do software

KiCad, como pode ser visto na figura 5, e foi transferida de um papel fotográfico para a placa de

fenolite utilizando uma fonte de calor, depois de resfriada, foi imersa em percloreto de ferro por

cerca de cinco minutos. Após o fim do processo, obtivemos uma placa funcional do circuito do

projeto, como pode ser visto na figura 6.


Figura 5 – Desenho do circuito no software KiCad.


Figura 6 – Placa produzida manualmente utilizando o processo de corrosão por percloreto de ferro.

Com exceção dos servo motores, os componentes são posicionados dentro da estrutura

impressa (caixa) através de pequenos parafusos, dando espaço ao posicionamento do módulo

MPU-6050 com sua placa orientada na horizontal, nos permitindo obter leituras precisas da

inclinação nos dois eixos de rotação da estrutura articulada, como também possibilitar a passagem

dos cabos sem prejudicar outros componentes.

### 3 SOFTWARE

3.1 FERRAMENTAS E BIBLIOTECAS

O código do controlador foi feito utilizando o IDE do arduino e as bibliotecas

"MPU6050_light"e "Servo", disponíveis para download pelo IDE. A primeira biblioteca re-

aliza a leitura dos sensores acelerômetro e giroscópio pelo barramento I2C do arduino, além

de combiná-los com um filtro complementar que será explicado a seguir. A segunda biblioteca

realiza o controle das posições dos servo motores por meio de um sinal PWM. Uma visão geral

do funcionamento do sistema é dada pelo fluxograma na figura 7.

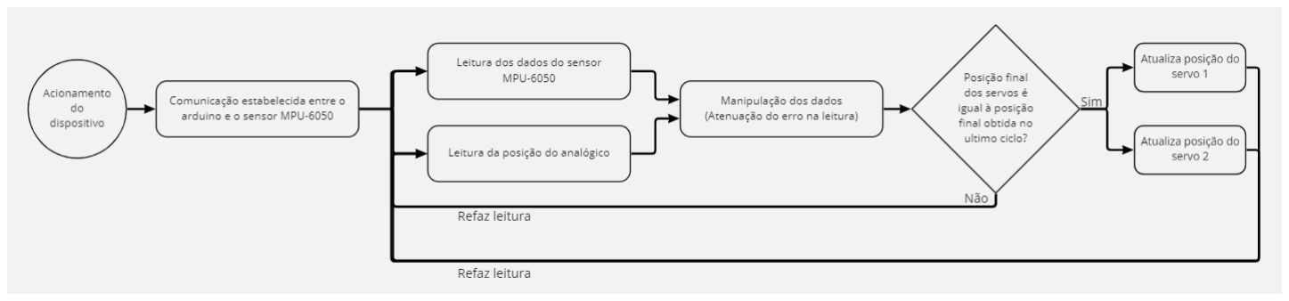
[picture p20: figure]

Figura 7 – Fluxograma da sequencia de operação do sistema.

3.2 ÂNGULOS A PARTIR DAS LEITURAS DO MPU-6050

A leitura dos sensores é realizada pela biblioteca "MPU6050_light", são lidos utilizando

o protocolo I2C os valores brutos da aceleração linear, do acelerômetro, e angular, do giroscópio.

Em funcionamento normal a maior aceleração linear percebida pelo dispositivo é a

gravidade e, com um pouco de trigonometria, é calculada a rotação do sistema em relação

à direção "para baixo". Ao longo do tempo o valor médio calculado se mantém próximo do

esperado, porém qualquer movimento, até mesmo as vibrações de origem térmica no material,

causam ruídos e ainda não podemos utilizar essa leitura diretamente.

Das leituras da aceleração angular podemos integrar o sinal duas vezes para obter a

velocidade angular e então o ângulo relativo à alguma posição de referência. Para um tempo

curto essa leitura já basta, contudo o erro do sistema é somado em cada ciclo de integração e

um desvio vai se acumulando com o tempo. Outro problema que precisa ser corrigido antes de

utilizar essa leitura é a definição dessa posição de referência.

Pode-se observar então que temos uma variável com boa confiança em curto

prazo (do giroscópio) e outra cuja a confiança é aceitável apenas após a coleta de várias leituras

após um longo tempo para ser calculada uma média (do acelerômetro). Pode-se então utilizar

a técnica de filtros complementares para combinar o sinal dos dois sensores e ter o melhor

dos dois mundos. A figura 8 apresenta um diagrama em blocos do filtro implementado pela

biblioteca. O parâmetro k controla qual medição vai ter mais influência em curto prazo e, por

complemento, qual teria mais influência após um tempo muito longo. Valores típicos são cerca

99%, dando um peso maior para as leituras de ângulo pelo giroscópio em curto prazo e para o

acelerômetro, que vai fazer o trabalho da posição de referência, após muito tempo.


Figura 8 – Operação do filtro - Imagem obtida na documentação da biblioteca "MPU6050_light"

3.3 TESTES SEM A ESTRUTURA 3D

Durante o desenvolvimento do projeto foi utilizada uma aplicação web 3d para testes

com sensor MPU-6050, que nos permitiu analisar seu funcionamento sem ter de acoplar motores

ou quaisquer outros atuadores, tal aplicação é executada no navegador Chrome ou semelhante do

computador, sendo necessário somente que o sensor esteja ligado a um arduino, e este arduino,

ligado ao computador. Ao iniciar a aplicação, é solicitada a porta serial conectada ao sistema

com o sensor, com isso, a interface fornece um cubo, como mostrado na figura 9, que acompanha

a rotação do sensor no mundo real.


Figura 9 – Fluxograma da sequencia de operação do sistema.

3.4 LEITURA DO JOYSTICK

No joystick é feito três leituras, o eixo x, eixo y e um botão de reset. Os eixos de

movimento são lidos direto por portas analógicas no arduino e o botão por uma porta digital.

O joystick controla um ajuste para cada eixo, esses ajustes são dois ângulos de desvio

a ser considerados no posicionamento dos motores. Movendo um eixo do joystick para uma

posição positiva o ajuste correspondente é incrementado com o tempo. O simétrico vale para

uma posição negativa também. Podemos imaginar um plano "Ajuste X x Ajuste Y"com um

ponto cujas as coordenadas são um ajuste final, o joystick então movimentaria esse ponto como

se fosse um personagem de um jogo.

3.5 CONTROLE DOS SERVOMOTORES

Os servomotores são controlados por um sinal modulado por largura de pulso (PWM).

O período do sinal é de 20ms e a largura de pulso varia entre 1ms e 2ms, que posicionam o servo

nas posições 0º e 180º, respectivamente. Para poupar tempo de desenvolvimento foi utilizada a

biblioteca "Servo"que gera essas formas de onda.

Da saída do filtro complementar já temos um bom posicionamento, mas ainda causa

solavancos extremos em quase todo movimento. Antes de enviar a nova posição de correção para

os servos esse sinal ainda é tratado com um filtro de média levando em conta os últimos 5 valores

e é adicionado o valor de ajuste do joystick. Então a posição do servomotor é interpolada entre a

posição antiga e a nova posição corrigida. Dessa forma no começo de uma correção os motores se

movimentam rapidamente e conforme se aproximam da posição final eles desaceleram, reduzindo

os solavancos.

### 4 RESULTADOS

4.1 HARDWARE

Os resultados obtidos com o protótipo do dispositivo evidenciaram que, para grandes

vibrações, o dispositivo funciona como esperado, anulando as inclinações indesejadas e

mantendo a estrutura articulada estável, o qual, junto dos sistemas de estabilização embutidos no

equipamento de vídeo, fornece uma imagem com poucas vibrações, oque já era esperado, uma

vez que o sistema estabiliza o suporte articulado dentro de limites de operação.

Foi observado que, movimentos bruscos de "grande amplitude"podem gerar

leituras fora dos padrões pelo sensor MPU-6050, com a grande maioria destas anormalidades

sendo anulada via software, porém, isso não se mostrou um problema, uma vez que o propósito

de um estabilizador externo é amenizar vibrações (como vibrações encontradas em um caminhar,

durante a gravação de um show ou outros eventos artísticos) e não balancear movimentos

demasiadamente grandes, que inclinem o equipamento mais que 90 graus para qualquer um dos

lados ou movimentos súbitos (como chacoalhar o equipamento ou coloca-lo de cabeça para

baixo).

4.2 SOFTWARE

Foi observado durante o desenvolvimento do projeto, dificuldade na integração das

leituras dadas pelo sensor MPU-6050 com os servo motores, posteriormente concluímos que o

problema quanto a rotação dos servos era a falta de um "filtro"para os valores obtidos pelo sensor,

a falta deste filtro ocasionava na tentativa de correção de orientação da estrutura articulada a cada

pequena variação na leitura do sensor, este, por possuir erro constante na leitura de cerca de 1

grau positivo ou negativo e uma nova leitura acontecendo a cada 20 milissegundos, ocasionava a

instabilidade de toda a estrutura articulada.

4.3 DESIGN FINAL

O design final do dispositivo pode ser visto nas figuras 10 e 11.

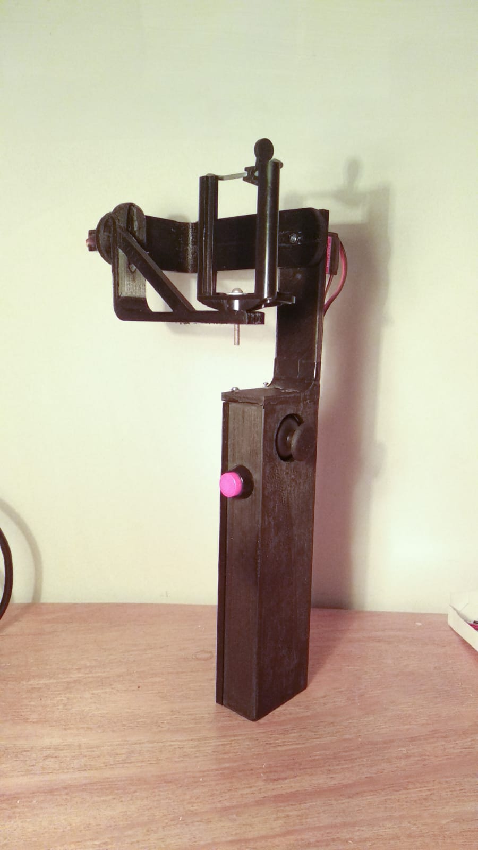
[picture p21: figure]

Figura 10 – Design final do dispositivo.

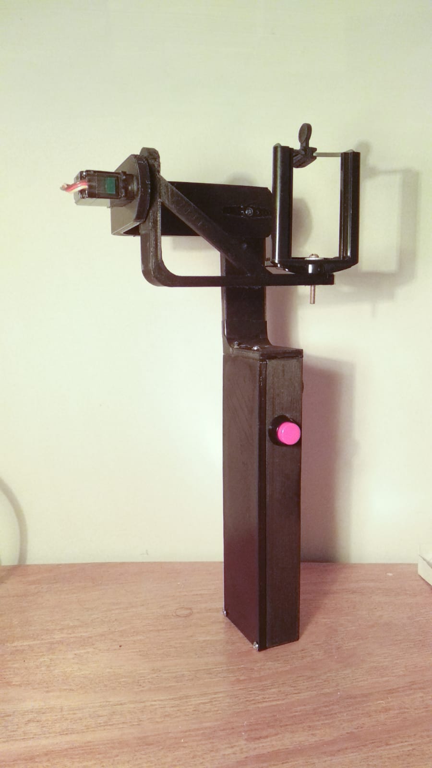
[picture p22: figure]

Figura 11 – Design final do dispositivo.

### 5 CONCLUSÕES

Apesar das dificuldades encontradas durante a construção e programação do dispositivo,

nota-se que, mesmo componentes de prototipação conseguem entregar um resultado aceitável.

Este projeto, mesmo sendo conceitualmente simples, se mostrou desafiador devido a possuir

partes móveis acopladas, oque a principio, gerou problemas de estabilidade e, no caso da estrutura

articulada, retrabalho de algumas peças. Além disso, o uso de ferramentas de edição 3d facilitou

muito o trabalho de construí-lo, assim como a visualização 3d das leituras do sensor por meio de

um software contribuiu para o entendimento do funcionamento do mesmo.

### 6 REFERENCIAS

Repositório de arquivos do projeto. Disponível em <https://github.com/ratatusznei/gimbal-

EEX21> Acessado durante todo o período de desenvolvimento do projeto.

Biblioteca MPU6050_light. Disponível em <https://github.com/rfetick/MPU6050_light>

Acessado durante todo o período de desenvolvimento do projeto.

Vídeo do projeto, ESTABILIZADOR DE DOIS EIXOS PARA CÂMERAS. Disponí-

vel em <https://youtu.be/y9m5s8JzXt0>

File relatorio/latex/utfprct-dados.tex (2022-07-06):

%% UTFPRCT-TEX, v1.0.6 wmeira on 2021/10/11
%% Copyright (C) 2020- by William H. T. Meira
%%
%% Modified version of project 'utfprpgtex' maintained 
%% by Luiz E. M. Lima
%%
%% This work may be distributed and/or modified under the
%% conditions of the LaTeX Project Public License, either version 1.3
%% of this license or (at your option) any later version.
%% The latest version of this license is in
%%   http://www.latex-project.org/lppl.txt
%% and version 1.3 or later is part of all distributions of LaTeX
%% version 2005/12/01 or later.
%%
%% This work has the LPPL maintenance status `maintained'.
%%
%% The Current Maintainer of this work is William H. T. Meira.
%%
%% This project consists mainly of files: 'utfprct.cls', 'utfprct.tex', 
%% 'utfprct-dados.tex' 
%% 
%% The 'abntex2-alf.bst' and 'abntex2-num.bst' files are slightly
%% modified versions of the bibtex styles from abntex2 (v.1.9.7)
%% package to suit NBR6023/2018 (not yet implemented there). 
%% Complementary, 'abntex2-alf-en.bst' and 'abntex2-num-en.bst' are
%% english versions of the respective bibtex styles.
%%
%% Contribute to improve this project (github repo):
%% https://github.com/wmeira/utfprct-tex

%%%%%%%%%%%%%%%%%%%%%%%%%%%%%%%%%%%%%%%%%%%%%%%
%%%%%%%%%%%%%%%%%%%%%%%%%%%%%%%%%%%%%%%%%%%%%%%
%% Tutorial do Documento de Dados 
%%%%%%%%%%%%%%%%%%%%%%%%%%%%%%%%%%%%%%%%%%%%%%%
%%
%% O 'utfprct-dados.tex' contém todos as informações do documento, 
%% metadados e outros valores importantes para o preenchimento dos 
%% elementos pré-textuais: capa, folha de rosto, resumo, abstract.
%% 
%% Não é necessário preencher todos os campos, existem campos mais
%% específicos para o tipo de documento sendo elaborado. Quando TCC,
%% por exemplo, não é necessário definir dados do programa de 
%% pós-graduação. Todos os dados inseridos estarão disponíveis para
%% inserção no tex usando o padrão '\imprimir + nomedodadominusculo'. 
%% Por exemplo, para imprimir o tipo do documento ('\TipoDeDocumento'),
%% usar '\imprimirtipodedocumento'.
%%
%% É possível customizar a descrição do documento na folha de rosto. 
%% Exemplos de descrição são fornecidos para guiar a escrita do texto,
%% em que pode-se utilizar os dados já definidos com o padrão descrito.
%%
%% Existe a possibilidade de inserir dados de uma instituição de 
%% cotutela quando se aplicar. 
%%
%% Os dados da ficha catalográfica são fornecidos pela biblioteca
%% e, na maioria das vezes, apenas anexa-se a folha digitalizada
%% na região definida dos elementos pré-textuais.
%%
%% A folha de aprovação é, na maioria das vezes, fornecido 
%% digitalmente pelo departamento ou pelo orientador após a defesa e 
%% deverá ser anexada ao documento na região definida dos elementos 
%% pré-textuais. Recomenda-se apenas anexar a folha de aprovação sem
%% precisar alterar os dados específicos aqui presentes, pois foram
%% criados originalmente para o template da folha de aprovação da
%% UTFPR-PG, presente no projeto base, e foram apenas mantidos.
%%
%%%%%%%%%%%%%%%%%%%%%%%%%%%%%%%%%%%%%%%%%%%%%%%
%%%%%%%%%%%%%%%%%%%%%%%%%%%%%%%%%%%%%%%%%%%%%%%

%%%%%%%%%%%%%%%%%%%%%%%%%%%%%%%%%%%%%%%%%%%%%%%
%% Informações do Documento
%%%%%%%%%%%%%%%%%%%%%%%%%%%%%%%%%%%%%%%%%%%%%%%

%% Tipo de documento (opções: "Tese", "Dissertação", "Trabalho de Conclusão de Curso"
\TipoDeDocumento{Oficina de integração 1 - Relatório Final}%copiar exatamente uma das opções 

%% [abstract] Document type: "Thesis", "Dissertation", "Bachelor Thesis"
%\DocumentType{Thesis}%

%% Nível de formação: "Doutorado", "Mestrado", "Bacharelado"
%\NivelDeFormacao{Doutorado}%

%% [abstract] Formation level: "Doctorate", "PhD", "Master's Degree", "Bachelor's Degree"
%\FormationLevel{PhD}%

%% Título ou grau pretendido: "Doutor", "Mestre" ou "Bacharel"
%\TituloPretendido{Doutor}%

%%%%%%%%%%%%%%%%%%%%%%%%%
%% Por padrão, o título principal será o \TituloDoDocumento (português)
%% Se a língua do documento for definida como inglês, será o \DocumentTitle

%% Título do documento em PORTUGUÊS (resumo)
\TituloDoDocumento{%%
EEX21_Equipe5_Relatório_EstabilizadorDeDoisEixosParaCâmeras
}%

%% Título em múltiplas linhas na capa, folha de rosto e termo de aprovação
%% Use o comando \par para indicar a quebra de linha
%%
%% A CAPA apresentará o título no formato de múltiplas linhas
%% para a respectiva língua do documento definida.
%%
%% Na folha de rosto, caso a língua do documento não seja português, aparecerá o
%% \TituloEmMultiplasLinhasIngles seguido pela tradução \TituloEmMultiplasLinhas
%%
\TituloEmMultiplasLinhas{%%
Estabilizador de dois eixos para câmeras
}%

\TituloEmMultiplasLinhasIngles{%%
\par
}%

%%%%%%%%%%%%%%%%%%%%%%%%%

%% Data da defesa
%\Dia{1}%% Dia (opcional: usado na ficha catalográfica apenas)
%\MesPorExtenso{janeiro}%% mês por extenso (opcional: usado na ficha catalográfica apenas)
\Ano{2022}%% Ano

%% Palavras-chave e keywords (máximo 5)
\NumeroDePalavrasChave{5}%% Número de palavras-chave 
\PalavraChaveA{Estabilizador para câmeras}%% Palavra-chave A
\PalavraChaveB{Servo motores}%% Palavra-chave B
\PalavraChaveC{Suporte articulado}%% Palavra-chave C
\PalavraChaveD{Manipulação de dados com arduino}%% Palavra-chave D
%\PalavraChaveE{Palavra-chave E}%% Palavra-chave E

\NumeroDeKeywords{\imprimirnumerodepalavraschave}%% Número de keywords (mesmo que palavras-chave)
\KeywordA{Keyword A}%% Keyword A
\KeywordB{Keyword B}%% Keyword B
\KeywordC{Keyword C}%% Keyword C
\KeywordD{Keyword D}%% Keyword D
\KeywordE{Keyword E}%% Keyword E

%%%%%%%%%%%%%%%%%%%%%%%%%%%%%%%%%%%%%%%%%%%%%%%
%% Informação do Autor(a) ou Autores(as) (TCC)
%%%%%%%%%%%%%%%%%%%%%%%%%%%%%%%%%%%%%%%%%%%%%%%

%%% Autor(a)
%% Usado para citação: "\SobrenomeDoAutor, PrenomeDoAutor" (ex: "Doe, John" ou "Doe, J.")
\NomeDoAutor{Henrique Francisco Knapp}%% Nome completo do(a) autor(a)
%\SobrenomeDoAutor{Último Nome}%% Último nome do(a) autor(a)
%\PrenomeDoAutor{Nome do(a) Autor(a) Sem Último}%% Nome do(a) autor(a) sem último nome

%%% Autor(a) 2 (opcional)
%% *Considera apenas se "\TipoDeDocumento" == "Trabalho de Conclusão de Curso"
\AtribuiAutorDois{true}%% Insere ou remove autor(a) 2: "true" ou "false"
\NomeDoAutorDois{Fernando Henrique Ratusznei Caetano}%% Nome completo do(a) autor(a) 2
%\SobrenomeDoAutorDois{Último Nome}%% Último nome do(a) autor(a) 2
%\PrenomeDoAutorDois{Nome do(a) Autor(a) 2 Sem Último}%% Nome do(a) autor(a) 2 sem último nome

%%% Autor(a) 3 (opcional)
%% *Considera apenas se "\TipoDeDocumento" == "Trabalho de Conclusão de Curso"
\AtribuiAutorTres{true}%% Insere ou remove autor(a) 3: "true" ou "false"
\NomeDoAutorTres{Robson Borges Dos Santos}%% Nome completo do(a) autor(a) 3
%\SobrenomeDoAutorTres{Último Nome}%% Último nome do(a) autor(a) 3
%\PrenomeDoAutorTres{Nome do(a) Autor(a) 3 Sem Último}%% Nome do(a) autor(a) 3 sem último nome

%%%%%%%%%%%%%%%%%%%%%%%%%%%%%%%%%%%%%%%%%%%%%%%%%%
%% Informações do Orientador(a) e Coorientador(a)
%%%%%%%%%%%%%%%%%%%%%%%%%%%%%%%%%%%%%%%%%%%%%%%%%%

%% Orientador(a)
%% Usado para citação: "\SobrenomeDoOrientador, PrenomeDoOrientador" (ex: "Doe, John" ou "Doe, J.")
\AtribuicaoOrientador{Orientador(a)}%% Atribuição "Orientador(a)"
\TituloDoOrientador{Prof(a). Dr(a).}%% Título do(a) orientador(a)
\NomeDoOrientador{Nome Completo do(a) Orientador(a)}%% Nome completo do(a) orientador(a)
\SobrenomeDoOrienador{Último Nome}%% Último nome do(a) orientador(a)
\PrenomeDoOrientador{Nome do(a) Orientador(a) Sem Último}%% Nome do(a) orientador(a) sem último nome

%% Coorientador(a) (opcional)
%% Usado para citação: "\SobrenomeDoCoorientador, PrenomeDoCoorientador" (ex: "Doe, John" ou "Doe, J.")
\AtribuiCoorientador{true}%% Insere ou remove o(a) coorientador(a): "true" ou "false"
\AtribuicaoCoorientador{Coorientador(a)}%% Atribuição "Coorientador(a)"
\TituloDoCoorientador{Prof(a). Dr(a).}%% Título do(a) coorientador(a)
\NomeDoCoorientador{Nome Completo do(a) Coorientador(a)}%% Nome completo do(a) coorientador(a)
\SobrenomeDoCoorienador{Último Nome}%% Último nome do(a) coorientador(a)
\PrenomeDoCoorientador{Nome do(a) Coorientador(a) Sem Último}%% Nome do(a) coorientador(a) sem último nome

%%%%%%%%%%%%%%%%%%%%%%%%%%%%%%%%%%%%%%%%%%%%%%%%%%
%% Informações da Instituição
%%%%%%%%%%%%%%%%%%%%%%%%%%%%%%%%%%%%%%%%%%%%%%%%%%

%% Nome da instituição
\Instituicao{Universidade Tecnológica Federal do Paraná}

%% [abstract] Institution name (*nome sem traduzir é o recomendado para docs. da UTFPR)
%\Institution{Universidade Tecnológica Federal do Paraná}

%% Sigla da Instituição
\SiglaInstituicao{UTFPR}

%% Nome da cidade (câmpus)
\Cidade{Curitiba}

%% Diretoria: "Graduação e Educação Profissional" ou "Pesquisa e Pós-Graduação" (opcional)
%\Diretoria{Pesquisa e Pós-Graduação}

%% Nome do departamento ou da coordenação (opcional: mais comum no Bacharelado: Departamento de Informática)
\Departamento{Curso de Engenharia de Computação}

%% Sigla do departamento (opcional, ex: DAINF, DAMEC, DAMAT...)
%\SiglaDepartamento{DPT}

%% Nome do curso bachalerado ou pós-graduação (PPG) (ex: "Engenharia de Computação",  "Engenharia El{\'e}trica e Inform{\'a}tica Industrial") 
\Curso{Engenharia de Computação}

%% Programa ou nome do curso completo (capa)
%% "Bachalerado em Engenharia de Computação"
%% "Programa de Pós-Graduação em Engenharia Elétrica e Informática Industrial"
\Programa{Programa de Pós-Graduação em \imprimircurso}

%% Sigla do programa de pós-graduação (opcional, ex: CPGEI, PPGCA)
\SiglaDoPPG{PPG}

%% Nome da área de concentração
\AreaDeConcentracao{Nome da Área de Concentração}

%%%%%%%%%%%%%%%%%%%%%%%%%%%%%%%%%%%%%%%%%%%%%%%%%%%%%%
%% Informações de Cotutela (Duplo Grau) (opcional)
%%%%%%%%%%%%%%%%%%%%%%%%%%%%%%%%%%%%%%%%%%%%%%%%%%%%%%

%% Insere dados de cotutela: "true" ou "false"
\AtribuiCotutela{false}

%% Nome da instituição de cotutela
\InstituicaoCotutela{Universidade Da Cotutela}

%% [abstract] Institution name
\InstitutionCotutela{Double Degree University}

%% Sigla da instituição de cotutela
\SiglaInstituicaoCotutela{UC}

%% Nome do departamento ou da coordenação da inst. de cotutela (mais comum no Bacharelado: Departamento de Informática)
\DepartamentoCotutela{Nome do Departamento ou da Coordenação}

%% Sigla do departamento da inst. cotutela (ex: DAINF, DAMEC, DAMAT...)
\SiglaDepartamentoCotutela{DPT-EXT}

%% Nome do curso bachalerado ou pós-graduação (PPG) na instituição de cotutela (ex: "Engenharia de Computação",  "Engenharia El{\'e}trica e Inform{\'a}tica Industrial")
\CursoCotutela{Nome do Curso Cotutela}

%% [abstract] Course name 
\CourseCotutela{Second Degree Course}

%% Programa ou nome do curso completo na inst. cotutela (capa)
%% "Bachalerado em Engenharia de Computação"
%% "Programa de Pós-Graduação em Engenharia Elétrica e Informática Industrial"
\ProgramaCotutela{Programa de Doutoral em \imprimircursocotutela}

%% Sigla do programa externo de pós-graduação
\SiglaDoPPGCotutela{PPG-EXT}

%% Nome da área de concentração na instituição de cotutela
\AreaDeConcentracaoCotutela{Nome da Área de Concentração}

%% Nível de formação que será fornecido na referência do doc.
\NivelDeFormacaoResumo{Duplo doutorado}
\FormationLevelAbstract{Double PhD}

%% Informacoes do orientador(a) na instituição de cotutela

%% Orientador(a) da instituição de cotutela
%% Usado para citação: "\SobrenomeDoOrientador, PrenomeDoOrientador" (ex: "Doe, John" ou "Doe, J.")
\AtribuicaoOrientadorCotutela{Orientador(a)}%% Atribuição "Orientador(a)"
\TituloDoOrientadorCotutela{Prof(a). Dr(a).}%% Título do(a) orientador(a)
\NomeDoOrientadorCotutela{Nome Completo do(a) Orientador(a)}%% Nome completo do(a) orientador(a)
\SobrenomeDoOrienadorCotutela{Último Nome}%% Último nome do(a) orientador(a)
\PrenomeDoOrientadorCotutela{Nome do(a) Orientador(a) Sem Último}%% Nome do(a) orientador(a) sem último nome

%% Coorientador(a) da instituição de cotutela
%% Usado para citação: "\SobrenomeDoCoorientador, PrenomeDoCoorientador" (ex: "Doe, John" ou "Doe, J.")
\AtribuiCoorientadorCotutela{false}%% Insere ou remove o(a) coorientador(a) da cotutela: "true" ou "false"
\AtribuicaoCoorientadorCotutela{Coorientador(a)}%% Atribuição "Coorientador(a)"
\TituloDoCoorientadorCotutela{Prof(a). Dr(a).}%% Título do(a) coorientador(a)
\NomeDoCoorientadorCotutela{Nome Completo do(a) Coorientador(a)}%% Nome completo do(a) coorientador(a)
\SobrenomeDoCoorienadorCotutela{Último Nome}%% Último nome do(a) coorientador(a)
\PrenomeDoCoorientadorCotutela{Nome do(a) Coorientador(a) Sem Último}%% Nome do(a) coorientador(a) sem último nome

%%%%%%%%%%%%%%%%%%%%%%%%%%%%%%%%%%%%%%%%%%%%%%%%%%
%% Folha de Rosto
%%%%%%%%%%%%%%%%%%%%%%%%%%%%%%%%%%%%%%%%%%%%%%%%%%

%% Descrição do documento na folha de rosto (exemplos)
\DescricaoDoDocumento{
Relatório final do projeto desenvolvido na disciplina de Oficina de Integração 1, do curso de Engenharia de Computação, da
Universidade Tecnológica Federal do Paraná (UTFPR).\\
\\Orientadores:\\Prof. Juliano Mourão Vieira.\\Prof. Ronnier Frates Rohrich
}

%% Insere ou remove descrição da cotutela (extra) na folha de rosto: "true" ou "false". 
%% Se "true", a descrição do documento será colocada na folha de rosto, logo abaixo do orientador(a) e coorientador(a) da primeira inst. e depois o orientador(a) e coorientador(a) da inst. de cotutela. 
%% Se "false", os nomes do orientador(a) e coorientador(a) aparecerão logo abaixo do orientador(a) da primeira instituição, sem uma descrição extra. Neste caso, recomenda-se revisar a "\DescricaoDoDocumento" para contemplar ambas as instituições.   
\AtribuiDescricaoCotutela{false}

%% Segunda Descricao da Inst. de Cotutela na folha de rosto (exemplos)
\DescricaoDoDocumentoCotutela{
\imprimirtipodedocumento\ apresentado(a) como requisito à obtenção do título de \imprimirtitulopretendido\ em \imprimircursocotutela, do \imprimirppgoudepartamentocotutela, da \imprimirinstituicaocotutela.  
\imprimirtipodedocumento\ apresentada à Comissão de Acompanhamento de Tese do Programa Doutoral em \imprimircursocotutela\ do \imprimirinstituicaocotutela\ (\imprimirsiglainstituicaocotutela) como requisito à obtenção de grau de \imprimirtitulopretendido\ na área de concentração \imprimirareadeconcentracaocotutela.
}

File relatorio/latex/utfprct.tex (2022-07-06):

%% UTFPRCT-TEX, v1.0.6 wmeira on 2021/10/11
%% Copyright (C) 2020- by William H. T. Meira
%%
%% Modified version of project 'utfprpgtex' maintained 
%% by Luiz E. M. Lima
%%
%% This work may be distributed and/or modified under the
%% conditions of the LaTeX Project Public License, either version 1.3
%% of this license or (at your option) any later version.
%% The latest version of this license is in 
%%   http://www.latex-project.org/lppl.txt
%% and version 1.3 or later is part of all distributions of LaTeX
%% version 2005/12/01 or later.
%%
%% This work has the LPPL maintenance status `maintained'.
%%
%% The Current Maintainer of this work is William H. T. Meira.
%%
%% This project consists mainly of files: 'utfprct.cls', 'utfprct.tex', 
%% 'utfprct-dados.tex' 
%% 
%% The 'abntex2-alf.bst' and 'abntex2-num.bst' files are slightly
%% modified versions of the bibtex styles from abntex2 (v.1.9.7)
%% package to suit NBR6023/2018 (not yet implemented there).
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
%%   memoir (similares): crop, fancyhdr, geometry, sidecap, subﬁgure, titlesec.
%%   abntex2: babel, bookmark, calc, enumitem, ifthen, hyperref, textcase.
%%   utfprct: abntex2cite, ae, algorithmic, amsmath, backref, breakurl, caption, subcaption, cmap, color, eepic, epic, epsfig, etoolbox, fancyhdr, fix-cm, fontenc, glossaries, graphics, graphicx, helvet, hyphenat, indentfirst, inputenc, lastpage, morewrites, nomencl, sfmath, sistyle, substr, times, xtab, pdfpages.

%% Pacotes adicionais (\usepackage[options]{package})
\usepackage{bigdelim, booktabs, colortbl, longtable, multirow}%% Ferramentas para tabelas
\usepackage{amssymb, amstext, amsthm, icomma}%% Ferramentas para linguagem matemática
\usepackage{pifont, textcomp, wasysym}%% Símbolos de texto
\usepackage{graphicx}
\usepackage{float}

% Refinamento tipográfico: diminui badboxes
\usepackage{microtype}%

%% Comandos personalizados (\newcommand{name}[num]{definition})
\newcommand{\cpp}{\texttt{C$++$}}%% C++
\newcommand{\latex}{\LaTeX}%% LaTeX
\newcommand{\ds}{\displaystyle}%% Tamanho normal das equações
\newcommand{\bsym}[1]{\boldsymbol{#1}}%% Texto no modo matemático em negrito
\newcommand{\mr}[1]{\mathrm{#1}}%% Texto no modo matemático normal (não itálico)
\newcommand{\der}{\mr{d}}%% Operador diferencial
\newcommand{\deri}[2]{\frac{\der#1}{\der#2}}%% Derivada ordinária
\newcommand{\derip}[2]{\frac{\partial#1}{\partial#2}}%% Derivada parcial
\newcommand{\pare}[1]{\left(#1\right)}%% Parênteses
\newcommand{\colc}[1]{\left[#1\right]}%% Colchetes
\newcommand{\chav}[1]{\left\lbrace#1\right\rbrace}%% Chaves
\newcommand{\sen}{\operatorname{sen}}%% Operador seno
\newcommand{\senh}{\operatorname{senh}}%% Operador seno hiperbólico
\newcommand{\tg}{\operatorname{tg}}%% Operador tangente
\newcommand{\tgh}{\operatorname{tgh}}%% Operador tangente hiperbólico  
\ifthenelse{\equal{\languagename}{english}}{%%
\newcommand{\nomeequacao}{Equation}
\newcommand{\nomeequacoes}{Equations}
}{%default pt
\newcommand{\nomeequacao}{Equação}
\newcommand{\nomeequacoes}{Equações}
}%  
\newcommand{\seqref}[1]{\nomeequacao~\eqref{#1}}%% Referência de uma única equação
\newcommand{\meqref}[1]{\nomeequacoes~\eqref{#1}}%% Referência de multiplas equações
\newcommand{\citep}[1]{\cite{#1}}%% Atalho para citação implícita
\newcommand{\citet}[1]{\citeonline{#1}}%% Atalho para citação explícita
\newcommand{\citepa}[1]{(\citeauthor{#1})}%% Atalho para citação implícita (somente autor)
\newcommand{\citeta}[1]{\citeauthoronline{#1}}%% Atalho para citação explícita (somente autor)
\newcommand{\citepy}[1]{(\citeyear{#1})}%% Atalho para citação implícita (somente ano)
\newcommand{\citety}[1]{\citeyear{#1}}%% Atalho para citação explícita (somente ano)

%allow fixed size on collums with text position
\newcolumntype{L}[1]{>{\raggedright\let\newline\\\arraybackslash\hspace{0pt}}m{#1}}
\newcolumntype{C}[1]{>{\centering\let\newline\\\arraybackslash\hspace{0pt}}m{#1}}
\newcolumntype{R}[1]{>{\raggedleft\let\newline\\\arraybackslash\hspace{0pt}}m{#1}}

%%%%%%%%%%%%%%%%%%%%%%%%%%%%%%%%%%%%%%%%%%%%%%%
%%%%%%%%%%%%%%%%%%%%%%%%%%%%%%%%%%%%%%%%%%%%%%%
%% Configuração das entradas
%%

%% Arquivo de dados do modelo de documento LaTeX para produção de trabalhos acadêmicos da UTFPR
\input{./utfprct-dados}%% Realize as modificações pertinentes no arquivo "utfprct-dados.tex"

%% Ferramenta para criação de índices
\makeindex%% Não comente esta linha

%% Ferramenta para criação de glossários
\makeglossaries%% Não comente esta linha

%% Entradas da lista de abreviaturas, siglas e acrônimos
\include{./PreTexto/entradas-acronimos}% Comente para remover este item

%% Entradas do glossário
\include{./PosTexto/entradas-glossario}% Comente para remover este item

%% Ferramenta para criação de nomenclaturas
\makenomenclature%% Não comente esta linha

%%%%%%%%%%%%%%%%%%%%%%%%%%%%%%%%%%%%%%%%%%%%%%%
%%%%%%%%%%%%%%%%%%%%%%%%%%%%%%%%%%%%%%%%%%%%%%%
%% Início do documento
%%
\begin{document}%% Não comente esta linha

%%%%%%%%%%%%%%%%%%%%%%%%%%%%%%%%%%%%%%%%%%%%%%%
%%%%%%%%%%%%%%%%%%%%%%%%%%%%%%%%%%%%%%%%%%%%%%%
%% Formatação de páginas de elementos pré-textuais
%%
\pretextual%% Não comente esta linha

%%%%%%%%%%%%%%%%%%%%%%%%%%%%%%%%%%%%%%%%%%%%%%%
%% Capa
%%
\incluircapa%% Comente para remover este item
%%%%%%%%%%%%%%%%%%%%%%%%%%%%%%%%%%%%%%%%%%%%%%%

%%%%%%%%%%%%%%%%%%%%%%%%%%%%%%%%%%%%%%%%%%%%%%%
%% Folha de rosto (comentar para remover pré-textual)
%%
%% A descrição da folha de rosto pode ser customizada no 
%% arquivo de dados ('utfprct-dados.tex) alterando o dado
%% '\DescricaoDoDocumento'. Colocando o * (asterisco)
%% insere a ficha catalográfica no verso da folha de rosto
%%
%% Licenciamento: a resolução conjunta Nº 01/2020 COGEP-COPPG torna
%% obrigatório a inclusão de uma das 6 licenças Creative Commons
%% disponíveis na folha de rosto. Verificar junto ao curso ou 
%% programa de pós-graduação qual deve ser utilizada no trabalho. 
%% Por exemplo, o CPGEI aderiu a CC-BY. 
%%
%% Opções: CC-BY, CC-BY-SA, CC-BY-ND, CC-BY-NC, CC-BY-NC-SA, CC-BY-NC-ND, Nenhuma
%%
\Licenca{CC-BY}
%\incluirfolhaderosto*%% Com ficha catalográfica no verso 
\incluirfolhaderosto%% Sem ficha catalográfica no verso
%%%%%%%%%%%%%%%%%%%%%%%%%%%%%%%%%%%%%%%%%%%%%%%

%%%%%%%%%%%%%%%%%%%%%%%%%%%%%%%%%%%%%%%%%%%%%%%
%% Resumo
%%
\include{./PreTexto/resumo}%% Comente para remover este item
%%%%%%%%%%%%%%%%%%%%%%%%%%%%%%%%%%%%%%%%%%%%%%%

%%%%%%%%%%%%%%%%%%%%%%%%%%%%%%%%%%%%%%%%%%%%%%%
%% Sumário
%%
\incluirsumario%% Comente para remover este item
%%%%%%%%%%%%%%%%%%%%%%%%%%%%%%%%%%%%%%%%%%%%%%%

%%%%%%%%%%%%%%%%%%%%%%%%%%%%%%%%%%%%%%%%%%%%%%%
%%%%%%%%%%%%%%%%%%%%%%%%%%%%%%%%%%%%%%%%%%%%%%%
%% Formatação de páginas de elementos textuais
%%
\textual%% Não comente esta linha

%% Parte
%\part{Introdução}%% Comente para remover este item

%% Capítulo
\include{./Capitulo1 - Introdução/capitulo1}%% Comente para remover este item

%% Parte
%\part{Desenvolvimento}%% Comente para remover este item

%% Capítulo
\include{./Capitulo2 - Hardware/capitulo2}%% Comente para remover este item

%% Capítulo
\include{./Capitulo3 - Software/capitulo3}%% Comente para remover este item

%% Capítulo
\include{./Capitulo4 - Resultados/capitulo4}%% Comente para remover este item

%% Parte
%\part{Conclusão}%% Comente para remover este item

%% Capítulo
\include{./Capitulo5 - Conclusões/capitulo5}%% Comente para remover este item

\include{./Capitulo6 - Referencias/capitulo6}

%% Capítulos após este comando criam marcadores do pdf na raiz
% \phantompart%% Comente para remover este item

%% Capítulo de exemplo
%\include{./CapituloExemplo/capituloexemplo}%% Comente para remover este item

%%%%%%%%%%%%%%%%%%%%%%%%%%%%%%%%%%%%%%%%%%%%%%%
%%%%%%%%%%%%%%%%%%%%%%%%%%%%%%%%%%%%%%%%%%%%%%%
%% Formatação de páginas de elementos pós-textuais
%%
\postextual%% Não comente esta linha

%%%%%%%%%%%%%%%%%%%%%%%%%%%%%%%%%%%%%%%%%%%%%%%
%% Arquivos de referências
%%
\arquivosdereferencias{%% Arquivos bibtex sem a extensão .bib e separados por vírgula - Não comente esta linha
  %./PosTexto/exemplos-referencias,%% Arquivo de referências - Comente para remover este item (chktex 26 supress warn.)
  %./PosTexto/referencias%% Arquivo de referências - Comente para remover este item (chktex 26 - supress warn.)
}%% Não comente esta linha
%%%%%%%%%%%%%%%%%%%%%%%%%%%%%%%%%%%%%%%%%%%%%%%

%% Fim do documento
\end{document}%% Não comente esta linha
%%%%%%%%%%%%%%%%%%%%%%%%%%%%%%%%%%%%%%%%%%%%%%%

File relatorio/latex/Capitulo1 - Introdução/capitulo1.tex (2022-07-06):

%%%% CAPÍTULO 1 - INTRODUÇÃO
%%
%% Deve apresentar uma visão global da pesquisa, 
%% incluindo: breve histórico, importância e
%% justificativa da escolha do tema, delimitações
%% do assunto, formulação de hipóteses e objetivos
%% da pesquisa e estrutura do trabalho.

%% Título e rótulo de capítulo (rótulos não devem conter caracteres especiais, acentuados ou cedilha)
\chapter{Introdução}\label{cap:introducao}

\section{Motivação}
Um recurso que está começando a se tornar popular em dispositivos de captura de vídeo apenas recentemente é a estabilização mecânica. Para pequenas vibrações, a estabilização eletrônica ou digital (já existente a alguns anos) já é suficiente para melhorar a qualidade de fotos, esta é feita via software, através de um algoritmo que tenta minimizar a vibração do dispositivo, no entanto, sua aplicação para vídeos ainda apresenta alguns problemas, uma vez que tal estabilização exige que cada quadro do vídeo seja trabalhado de forma diferente pelo algoritmo, de modo que a gravação final tenha uma boa estabilização, o que pode custar muito do processamento de um dispositivo. Outro mecanismo existente é a estabilização óptica, que, através de sensores embutidos no dispositivo, identifica os movimentos realizados, e através de pequenos motores, ajusta a posição das lentes de modo a obter imagens mais estáveis durante a gravação. Esta é uma solução melhor que a típica estabilização digital presente na maioria dos dispositivos de gravação, como celulares e pequenas câmeras, mas ainda é um recurso com limitações, e para dar a um dispositivo a melhor estabilização possível, foi criado um equipamento externo para realizar esta função.\\
\indent A estabilização mecânica realizada por um dispositivo externo não possui as limitações de movimentação do dispositivo de gravação, mesmo que a base onde o estabilizador externo é fixado se mova, sua estrutura articulada realiza os movimentos contrários aos realizados pela base, anulando os movimentos e deixando o dispositivo anexado a esta estrutura estabilizado. Este é um recurso caro e economicamente indisponível para a grande parte das pessoas.

\section{Objetivos}

    \subsection{Objetivo geral}
    Criação de um dispositivo de estabilização externa que possua uma estrutura articulada que se movimente em dois eixos, de modo a deixar sua base acoplada, estabilizada, e como consequência, o dispositivo de vídeo anexado a esta base, também estabilizado. Tal equipamento deve ser composto por atuadores e sensores acoplados à um microcontrolador Arduino.
    
    \subsection{Objetivos específicos}
    
        \begin{itemize}
            \item O equipamento deve operar com baterias, estas devem ser carregadas externamente.
            \item O equipamento deve estabilizar uma base através da movimentação de dois eixos de rotação, um eixo mantendo a inclinação vertical, e outro eixo mantendo a inclinação horizontal.
            \item O equipamento deve permitir a mudança de orientação da base (onde é fixado o dispositivo externo) através de um joystick analógico, com o switch tendo a função de posicionar a base de volta a posição original.
            \item A base presa à estrutura articulada deve possibilitar anexar um smartphone ou uma câmera externa com peso de até 300 gramas, sendo esse valor definido pela resistência tolerada pela estrutura impressa.
            \item Deve ser feita uma placa de circuito específica para o dispositivo.
            \item A estrutura do equipamento deve ser produzida por uma impressora 3D.
        \end{itemize}

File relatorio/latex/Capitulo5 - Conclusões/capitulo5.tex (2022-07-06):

%%%% CAPÍTULO 5 - CONCLUSÕES E PERSPECTIVAS
%%
%% Deve finalizar o trabalho com uma resposta às
%% hipóteses especificadas na introdução. O autor deve
%% manifestar seu ponto de vista sobre os resultados
%% obtidos; não se deve incluir neste capítulo novos
%% dados ou equações. A partir da tese, alguns assuntos
%% que foram identificados como importantes para serem
%% explorados poderão ser sugeridos como temas para
%% novas pesquisas.

%% Título e rótulo de capítulo (rótulos não devem conter caracteres especiais, acentuados ou cedilha)
\chapter{Conclusões}\label{cap:conclusoeseperspectivas}

Apesar das dificuldades encontradas durante a construção e programação do dispositivo, nota-se que, mesmo componentes de prototipação conseguem entregar um resultado aceitável. Este projeto, mesmo sendo conceitualmente simples, se mostrou desafiador devido a possuir partes móveis acopladas, oque a principio, gerou problemas de estabilidade e, no caso da estrutura articulada, retrabalho de algumas peças. Além disso, o uso de ferramentas de edição 3d facilitou muito o trabalho de construí-lo, assim como a visualização 3d das leituras do sensor por meio de um software contribuiu para o entendimento do funcionamento do mesmo.

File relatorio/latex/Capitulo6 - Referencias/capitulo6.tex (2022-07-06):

\chapter{Referencias}

\phantom{aaa}\\
Repositório de arquivos do projeto. Disponível em <https://github.com/ratatusznei/gimbal-EEX21> Acessado durante todo o período de desenvolvimento do projeto.\\\\
Biblioteca MPU6050\textunderscore light. Disponível em <https://github.com/rfetick/MPU6050\textunderscore light> Acessado durante todo o período de desenvolvimento do projeto.\\\\
Vídeo do projeto, ESTABILIZADOR DE DOIS EIXOS PARA CÂMERAS. Disponível em <https://youtu.be/y9m5s8JzXt0>

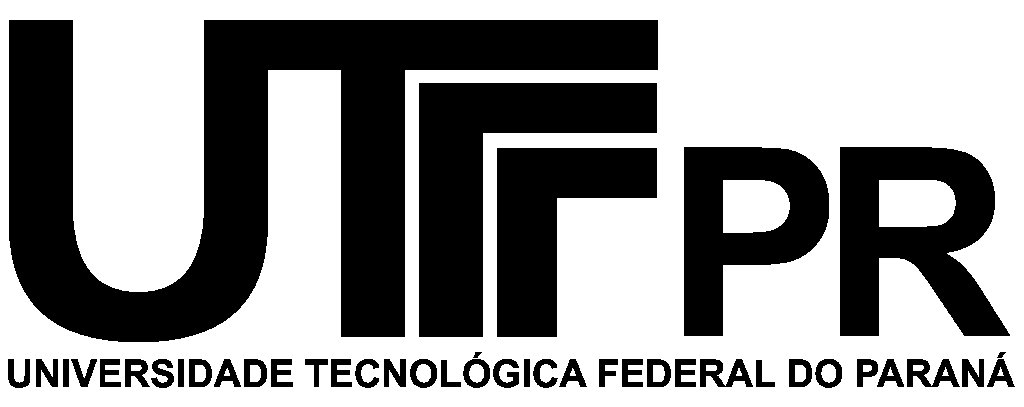
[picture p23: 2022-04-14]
board/project/images/utfpr.png

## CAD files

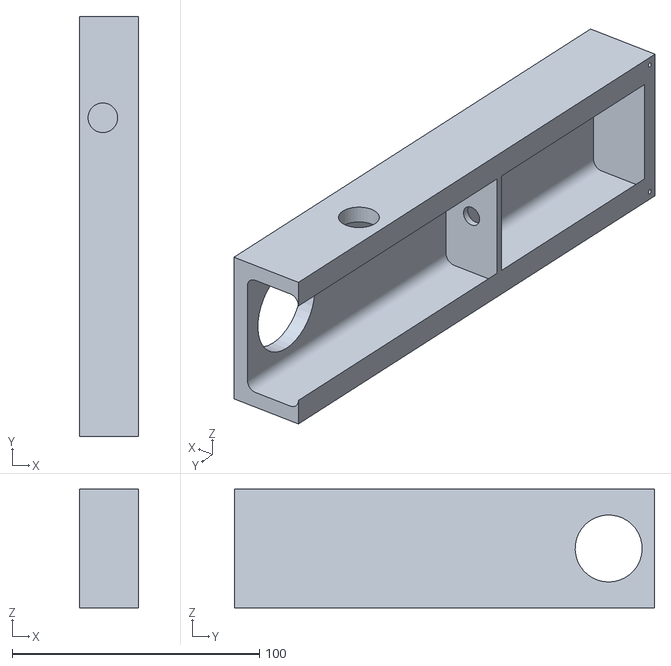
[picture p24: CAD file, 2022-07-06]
structure-3d/caixa.stl
24.0 x 170.0 x 48.0

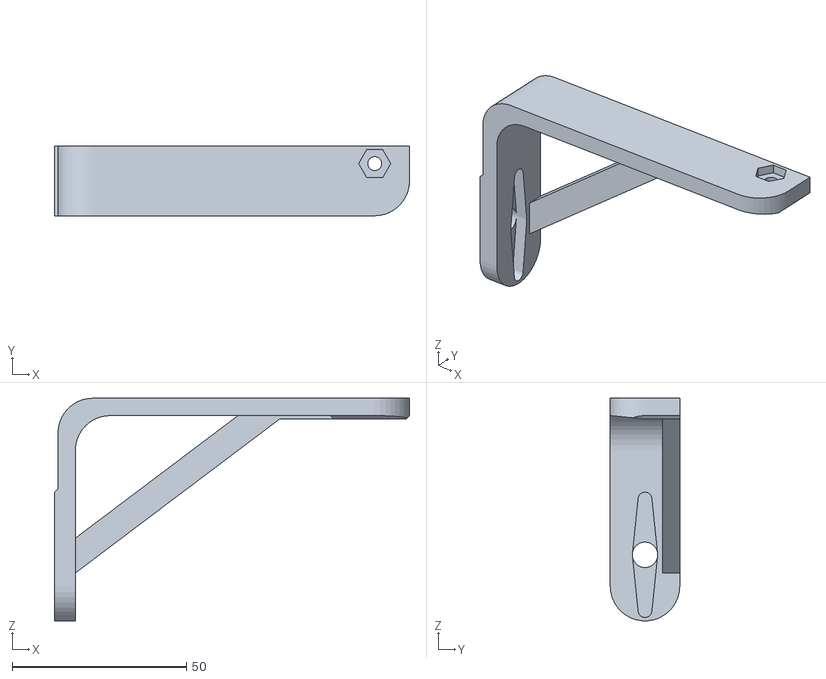
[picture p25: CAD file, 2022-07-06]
structure-3d/braco_menor.stl
102.0 x 20.0 x 64.0

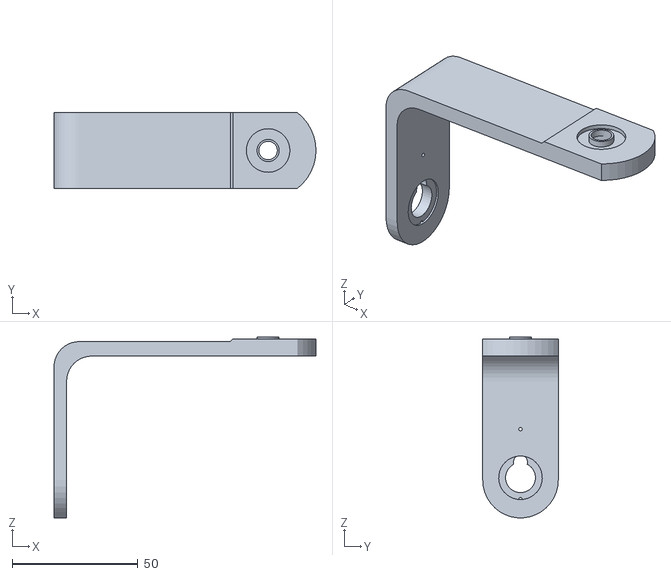
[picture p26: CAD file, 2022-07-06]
structure-3d/braco_maior.stl
104.0 x 30.0 x 71.7

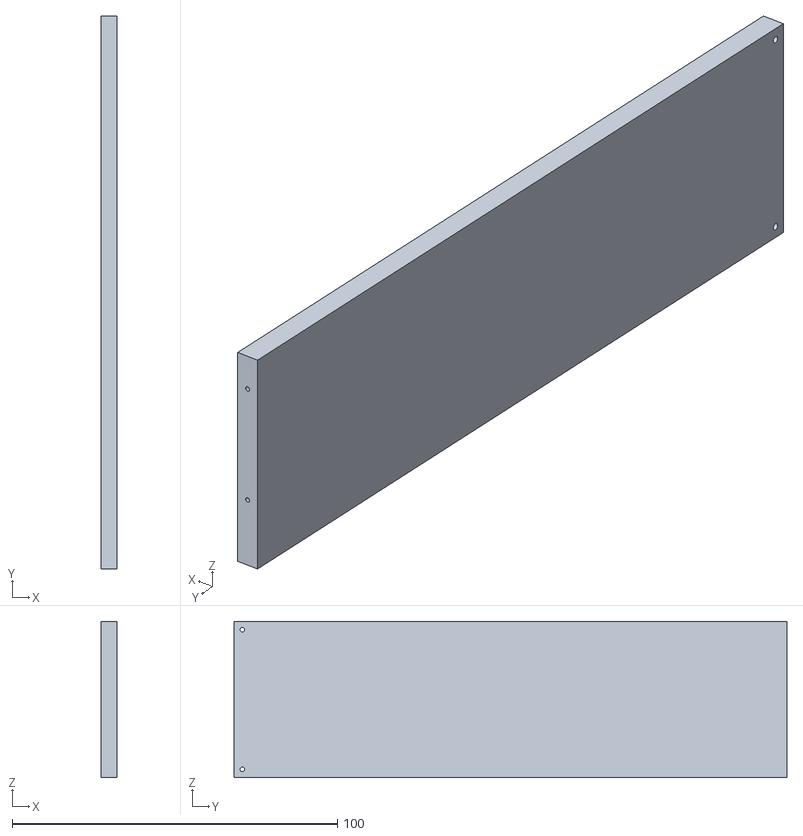
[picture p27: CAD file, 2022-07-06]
structure-3d/tampa.stl
5.00 x 170.0 x 48.0

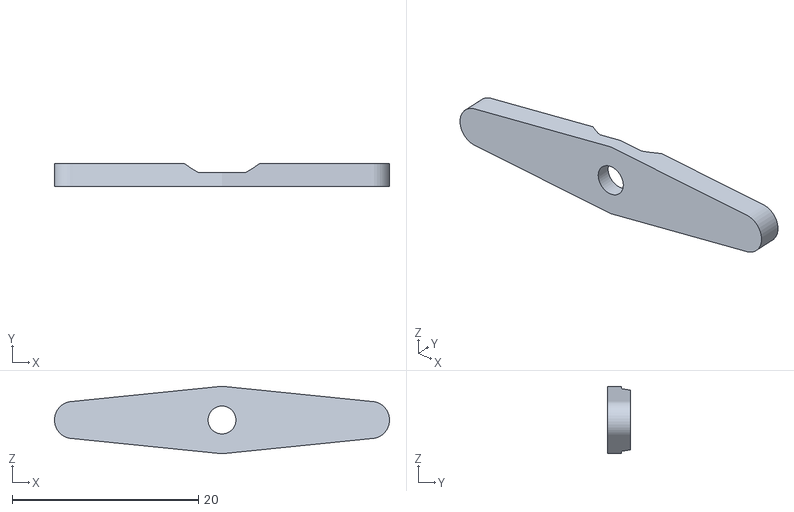
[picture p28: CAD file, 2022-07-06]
structure-3d/tampinha_x2.stl
36.0 x 2.52 x 7.25

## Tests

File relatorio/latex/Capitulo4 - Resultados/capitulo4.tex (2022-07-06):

%%%% CAPÍTULO 4 - RESULTADOS E DISCUSSÃO
%%
%% Deve descrever detalhadamente os dados obtidos 
%% pelo autor. Normalmente são incluídas ilustrações
%% como: quadros, tabelas, gráficos, etc. Deve efetuar
%% a comparação dos dados obtidos e/ou resultados, com
%% aqueles descritos na revisão de literatura, 
%% incluindo os comentários sobre os estudos de outros
%% autores.

%% Título e rótulo de capítulo (rótulos não devem conter caracteres especiais, acentuados ou cedilha)
\chapter{Resultados}\label{cap:resultadosediscussao}

\section{Hardware}
Os resultados obtidos com o protótipo do dispositivo evidenciaram que, para grandes vibrações, o dispositivo funciona como esperado, anulando as inclinações indesejadas e mantendo a estrutura articulada estável, o qual, junto dos sistemas de estabilização embutidos no equipamento de vídeo, fornece uma imagem com poucas vibrações, oque já era esperado, uma vez que o sistema estabiliza o suporte articulado dentro de limites de operação.\\
\\
\indent Foi observado que, movimentos bruscos de "grande amplitude" podem gerar leituras fora dos padrões pelo sensor MPU-6050, com a grande maioria destas anormalidades sendo anulada via software, porém, isso não se mostrou um problema, uma vez que o propósito de um estabilizador externo é amenizar vibrações (como vibrações encontradas em um caminhar, durante a gravação de um show ou outros eventos artísticos) e não balancear movimentos demasiadamente grandes, que inclinem o equipamento mais que 90 graus para qualquer um dos lados ou movimentos súbitos (como chacoalhar o equipamento ou coloca-lo de cabeça para baixo).

\section{Software}
Foi observado durante o desenvolvimento do projeto, dificuldade na integração das leituras dadas pelo sensor MPU-6050 com os servo motores, posteriormente concluímos que o problema quanto a rotação dos servos era a falta de um "filtro" para os valores obtidos pelo sensor, a falta deste filtro ocasionava na tentativa de correção de orientação da estrutura articulada a cada pequena variação na leitura do sensor, este, por possuir erro constante na leitura de cerca de 1 grau positivo ou negativo e uma nova leitura acontecendo a cada 20 milissegundos, ocasionava a instabilidade de toda a estrutura articulada.

\section{Design final}
O design final do dispositivo pode ser visto nas figuras 10 e 11.

\begin{figure}[H]
\centering
\\
\caption{\label{fig:widgets}Design final do dispositivo.}
\end{figure}

\begin{figure}[H]
\centering
\\
\caption{\label{fig:widgets}Design final do dispositivo.}
\end{figure}

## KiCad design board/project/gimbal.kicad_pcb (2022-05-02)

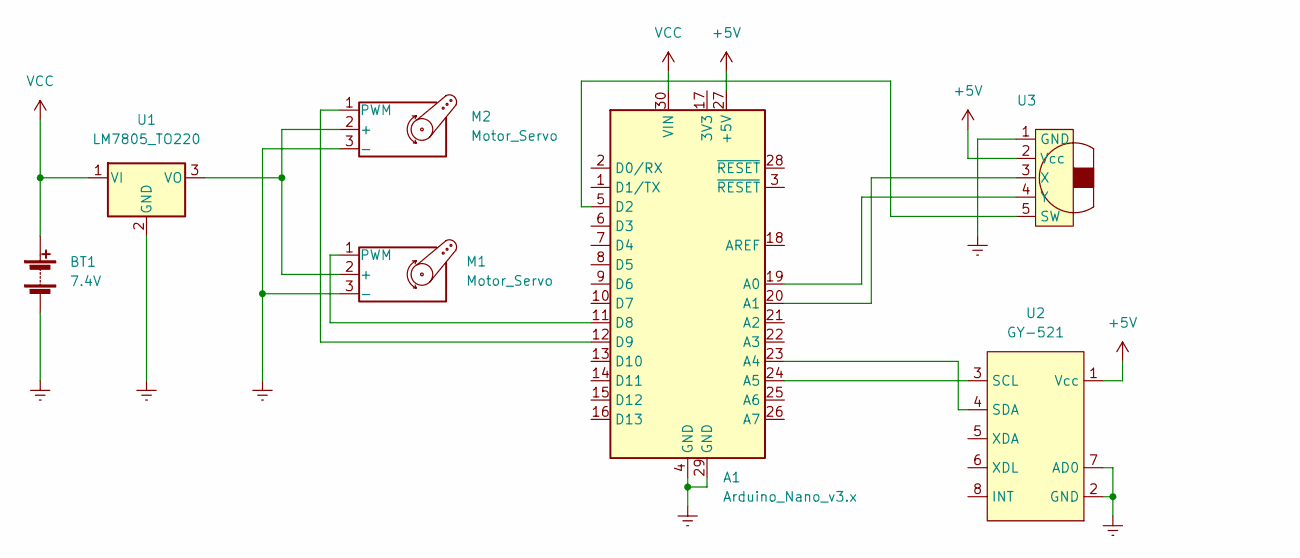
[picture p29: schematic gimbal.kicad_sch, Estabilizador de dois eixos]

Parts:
A1: Arduino_Nano_v3.x; Arduino_Nano
BT1: 7.4V; PinHeader_1x02_P2.54mm_Vertical
M1, M2: Motor_Servo; PinHeader_1x03_P2.54mm_Vertical
U1: LM7805_TO220; TO-220-3_Vertical
U2: GY-521; PinSocket_1x08_P2.54mm_Vertical
U3: (no value)

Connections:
+5V: A1.27 (+5V), U2.1 (Vcc), U3.2 (Vcc)
Earth: A1.4 (GND), A1.29 (GND), BT1.2 (-), M1.3 (-), M2.3 (-), U1.2 (GND), U2.2 (GND), U2.7 (AD0), U3.1 (GND)
unnamed: A1.5 (D2), U3.5 (SW)
unnamed: A1.11 (D8), M1.1 (PWM)
unnamed: A1.12 (D9), M2.1 (PWM)
unnamed: A1.19 (A0), U3.4 (Y)
unnamed: A1.20 (A1), U3.3 (X)
unnamed: A1.23 (A4), U2.4 (SDA)
unnamed: A1.24 (A5), U2.3 (SCL)
unnamed: M1.2 (+), M2.2 (+), U1.3 (VO)
VCC: A1.30 (VIN), BT1.1 (+), U1.1 (VI)

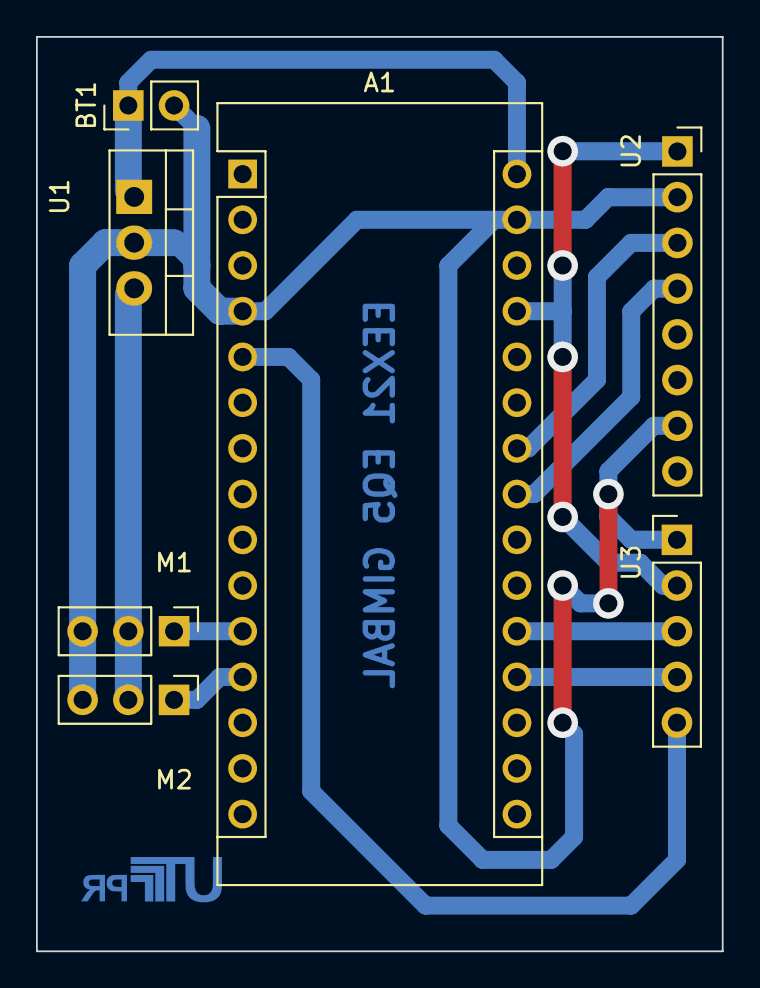
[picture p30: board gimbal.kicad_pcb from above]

Board: 2 copper layers, 38.1 x 50.8 mm, 8 parts (1 on the bottom side), 11 nets.

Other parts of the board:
Logo: LOGO; utfpr

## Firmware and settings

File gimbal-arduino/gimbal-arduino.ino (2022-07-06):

#include "Imu.hpp"
#include "ServoController.hpp"
#include "Joystick.hpp"

/*
Sequencia de funcionamento (loop):
  1.Coleta dos dados do sensor MPU6050
  2.Leitura do joystick analogico
  3.Operações sobre os dados lidos + variação analogicos
    -Partindo sempre da posição de calibração, a cada loop serão calculadas as inclinações + variação desejada,
    de modo que a cada loop teremos novos valores para o posicionamentos dos servos.
    -A variação lida do joystick em qualquer loop deve permanecer após o fim do mesmo.
  4.Saída para os servos
    -Com limitantes de velocidade (sem guinadas -> movimentação suave dentro dos limites de velocidade)
*/

Imu imu;
ServoController servos;
Joystick joystick;

void setup() {
	Serial.begin(115200);
	imu.begin();
	servos.begin();
	joystick.begin();
}

void loop() {
	imu.update();
	joystick.update();
	servos.set_target(
		imu.get_correction_x() + joystick.get_offset_x(),
		imu.get_correction_y() + joystick.get_offset_y()
	);
	servos.update();

	servos.print();
}

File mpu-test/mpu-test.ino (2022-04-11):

#include "I2Cdev.h"
#include "MPU6050_6Axis_MotionApps_V6_12.h"
#include <Servo.h>

/*
Sequencia de funcionamento (loop):
  1.Coleta dos dados do sensor MPU6050
  2.Leitura do joystick analogico
  3.Operações sobre os dados lidos + variação analogicos
    -Partindo sempre da posição de calibração, a cada loop serão calculadas as inclinações + variação desejada,
    de modo que a cada loop teremos novos valores para o posicionamentos dos servos.
    -A variação lida do joystick em qualquer loop deve permanecer após o fim do mesmo.
  4.Saída para os servos
    -Com limitantes de velocidade (sem guinadas -> movimentação suave dentro dos limites de velocidade)
*/

// imagens do acelerometro:
//https://bdm.unb.br/bitstream/10483/23639/1/2018_EduardoSousaSalesRodrigues_tcc.pdf


Servo s1;
Servo s2;

const int VRx = A0;
const int VRy = A1;
const int SW = 2;

MPU6050 mpu;
Quaternion q;
float euler[3]{ 0 };
float offset[3]{ 0 };

// MPU control/status vars
bool dmpReady = false;  // set true if DMP init was successful
uint8_t devStatus;      // return status after each device operation (0 = success, !0 = error)
uint16_t packetSize;    // expected DMP packet size (default is 42 bytes)
uint8_t fifoBuffer[64]; // FIFO storage buffer

float readJoystick (int pos, float& out) {
	if (pos > 20) {
		out += .1;
		if (out > 60) {
			out = 60;
		}
	}
	if (pos < -60) {
		out -= .1;
		if (out < -60) {
			out = -60;
		}
	}
}

void setup() {
	Serial.begin(115200);
	while (!Serial);

	Serial.println(F("Initializing I2C devices..."));
	mpu.initialize();

	Serial.println(F("Testing device connections..."));
	Serial.println(mpu.testConnection() ? F("MPU6050 connection successful") : F("MPU6050 connection failed"));

	delay(2000);
	Serial.println(F("Initializing DMP..."));
	devStatus = mpu.dmpInitialize();

	mpu.setXGyroOffset(51);
	mpu.setYGyroOffset(8);
	mpu.setZGyroOffset(21);
	mpu.setXAccelOffset(1150);
	mpu.setYAccelOffset(-50);
	mpu.setZAccelOffset(1060);

	if (devStatus == 0) {
		mpu.CalibrateAccel();
		mpu.CalibrateGyro();
		mpu.PrintActiveOffsets();

		Serial.println(F("Enabling DMP..."));
		mpu.setDMPEnabled(true);
		Serial.println(F("DMP ready!"));
		dmpReady = true;

		packetSize = mpu.dmpGetFIFOPacketSize();
		mpu.setRate(10); // 1kHz / (n + 5)
	} else {
		// ERROR!
		// 1 = initial memory load failed
		// 2 = DMP configuration updates failed
		// (if it's going to break, usually the code will be 1)
		Serial.print(F("DMP Initialization failed (code "));
		Serial.print(devStatus);
		Serial.println(F(")"));
	}

	s1.attach(8);
	s2.attach(9);

	pinMode(VRx, INPUT);
	pinMode(VRy, INPUT);
	pinMode(SW, INPUT_PULLUP); 
}

void loop() {
	if (!dmpReady) return;

	if (mpu.dmpGetCurrentFIFOPacket(fifoBuffer)) {
		mpu.dmpGetQuaternion(&q, fifoBuffer);
		/* Serial.print("{\"w\":");
		   Serial.print(q.w);
		   Serial.print(",\"x\":");
		   Serial.print(q.x);
		   Serial.print(",\"y\":");
		   Serial.print(q.y);
		   Serial.print(",\"z\":");
		   Serial.print(q.z);
		   Serial.println("}"); */

		mpu.dmpGetEuler(euler, &q);
		s1.write(120*(-euler[0] + 1.) + offset[0]);
		s2.write(120*(euler[1] + 1.) + offset[1]);
	}

	if(digitalRead(SW) == LOW) {
		offset[0] = 0;
		offset[1] = 0;
		offset[2] = 0;
	}

	int posicaoX = map(analogRead(VRx), 0, 1023, -200, 200);
	int posicaoY = map(analogRead(VRy), 0, 1023, -200, 200);

	readJoystick(posicaoX, offset[0]);
	readJoystick(posicaoY, offset[1]);
}

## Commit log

2022-04-11 joystick + servos
2022-04-14 logo + name + smaller board
    [gimbal.kicad_pcb]
2022-05-02 fix joystick power input
    [gimbal.kicad_pcb, gimbal.kicad_sch]
2022-05-12 move source to gimbal-arduino
2022-05-16 add 2nd servo
2022-05-16 imu class + makefile
2022-05-16 add servo controller
2022-05-28 filtro de media, ultimos 5 valores
2022-07-06 adiona arquivos stl da estrutura 3d
    [braco_maior.stl, braco_menor.stl, caixa.stl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]
